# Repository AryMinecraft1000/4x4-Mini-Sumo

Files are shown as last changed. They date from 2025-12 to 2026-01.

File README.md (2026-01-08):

# 4x4-Mini-Sumo
A 4x4 mini sumo robot to fit in the 10x10cm, 500g class.
I chose this design philosophy as I've built 2 wheel drive international competition winning robots before and I wanted to challenge myself with the added complexity and space restrictions of a 4x4 robot. I also want to use this design to compete im my local international competition this spring.

I'd like to note that this is **NOT a battlebot**, its a far **more complex** robot witch uses sensors and **advanced code** to execute its task (Unlike battlebots which are just rc cars with weapons). It is part of one of the most competitive classes in international robotics where the top robots cost well over 1000$.





The Jsumo PCB has wiring intructions written on it.



# Bill of Materials: Mini Sumo Robot Project

| Part Name | Unit Price (USD) | Qty | Total Price (USD) | URL |
| :--- | :---: | :---: | :---: | :--- |
| **Jsumo XMotion** All In One Controller V3 | $44.95 | 1 | $44.95 | [Link](https://www.jsumo.com/xmotion-robot-controller) |
| **Jsumo Mini Katana Blade** (10cm) | $4.95 | 2 | $9.90 | [Link](https://www.jsumo.com/mini-katana-blade-for-mini-sumo-robot-10cm) |
| **Jsumo JS40F** Digital Distance Sensor | $12.50 | 4 | $50.00 | [Link](https://www.jsumo.com/js40f-digital-infrared-ir-distance-sensor-min-40-cm-range) |
| **Jsumo JS2622S** Steel-Silicone Wheel Pair | $14.50 | 2 | $29.00 | [Link](https://www.jsumo.com/js2622-steel-silicone-wheel-pair-26mm-diameter) |
| **Generic 050 Motor** | $5.00 | 4 | $20.00 | [Link](https://www.aliexpress.com/item/1005008126068612.html) |
| **QRE1113 IR Reflection Sensor** | *Region Dep.* | 2 | $0.00* | [Link](https://www.aliexpress.com/item/1005005682098178.html) |
| **LiPo Battery** (Locally Sourced) | $20.00 | 1 | $20.00 | - |
| **Total Project Items** | - | - | **$173.85** | - |

---

### 📦 Final Cost Breakdown

| Description | Amount (USD) |
| :--- | ---: |
| Imported Jsumo Subtotal | $133.85 |
| Jsumo Shipping | $46.95 |
| Import Tax (23% of $180.80) | $41.58 |
| AliExpress Parts & Shipping | $35.00 |
| Local Battery (Exempt) | $20.00 |
| **GRAND TOTAL** | **$277.38** |

> [!NOTE]
> *The 23% import tax is only applied to Jsumo items and their respective shipping. AliExpress and local items are added as flat costs.

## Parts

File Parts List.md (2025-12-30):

For this project you will need:
- All the parts in the BOM
- All the 3D printed parts in the CAD file in their specified quantities
- one 2mm diamater axel between 35-50mm in length **(50mm recomended)**
- at least 1 spring with a **maximum lenght** of 11mm
- wires, however more than enough should be included with the Jsumo sensors
- conectors for the battery, **JST prefered** (one set, male and female)
- 8x 19mm long M3 screws for the motor covers/mounts **(thread lenght)**
- 4x 9mm long M2 screws for mounting the front walls **(thread lenght)**
- 2x 12mm long M2 screws for the whing-blade mechanism **(thread lenght)**
- 2x 6mm long M2 screws for mounting the front cover **(thread lenght)**
- 2x 4mm long M2 screws for mounting side sensors **(full lenght)**
- 2x 5mm long M2 screws for mounting front sensors **(full lenght)**
- 4x M2 nuts

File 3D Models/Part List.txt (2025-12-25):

Blade Bracket -> 1
Front Plate -> 1
IR Sensor Holder 1 -> 2
IR Sensor Holder 2 -> 2
Front Wall L -> 1
Front Wall R -> 1
Motor Cover -> 4
Chassis -> 1

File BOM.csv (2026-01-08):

Item | Description | Quantity | Unit Price ($) | Total Price ($) | URL
Jsumo XMotion | All In One Controller V3 | 1 | 44.95 | 44.95 | https://www.jsumo.com/xmotion-robot-controller
Jsumo Katana Blade | 10cm Mini Sumo Blade | 2 | 4.95 | 9.90 | https://www.jsumo.com/mini-katana-blade-for-mini-sumo-robot-10cm
Jsumo JS40F | Digital Distance Sensor | 4 | 12.50 | 50.00 | https://www.jsumo.com/js40f-digital-infrared-ir-distance-sensor-min-40-cm-range
Jsumo JS2622S | Steel-Silicone Wheel Pair | 2 | 14.50 | 29.00 | https://www.jsumo.com/js2622-steel-silicone-wheel-pair-26mm-diameter
050 Motor | Generic DC Motor | 4 | 5.00 | 20.00 | https://www.aliexpress.com/item/1005008126068612.html
QRE1113 IR Sensor | Infrared Reflection Sensor | 2 | Depending on Region | 0.00 | https://www.aliexpress.com/item/1005005682098178.html
AliExpress Shipping | Shipping for Motors/Sensors | 1 | 15.00 | 15.00
Jsumo Shipping | International Shipping Fee | 1 | 46.95 | 46.95
Import Tax | 23% Import Duty (Jsumo Only) | 1 | 41.58 | 41.58
LiPo Battery | Locally Sourced Battery | 1 | 20.00 | 20.00
FINAL TOTAL |  |  | 277.38

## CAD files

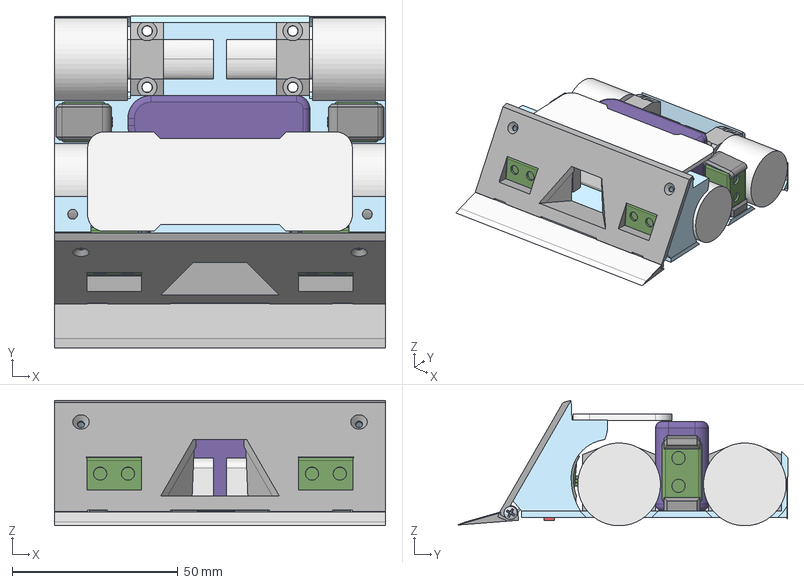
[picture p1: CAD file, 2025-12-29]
3D Models/4x4 Mini Sumo.step
100.0 x 100.2 x 37.9 mm
RR Motor
Part 1-Mirrored
RF Motor
Blade x 2
Chasis Base
XmotionV3
LR Motor
370mah 3s LiPo
IR Sensor Holder x 2
JS40F Digital Distance Sensor x 4
Line Sensor x 2
LF Motor
IR Sensor Holder 2 x 2
PH Pan head screw M2x0.40 x 16 x 2
Hex nut grade A & B M2x0.4 x 2
Blade Bracket Ver 2
torsion spring
Plow Shaft
Front Plate

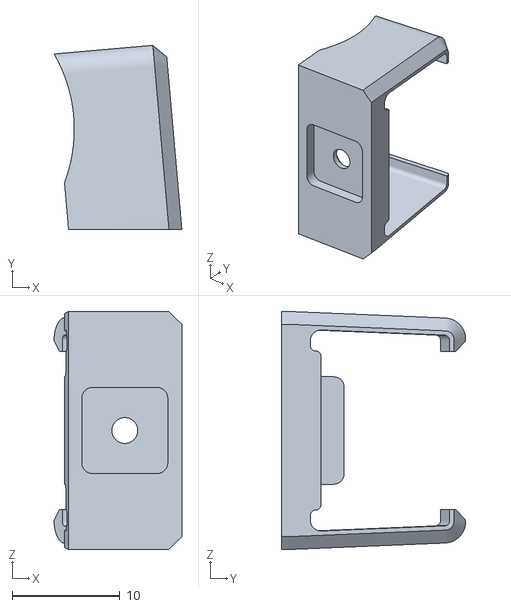
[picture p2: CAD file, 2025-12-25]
3D Models/IR Sensor Holder 2.stl
11.9 x 17.1 x 22.1

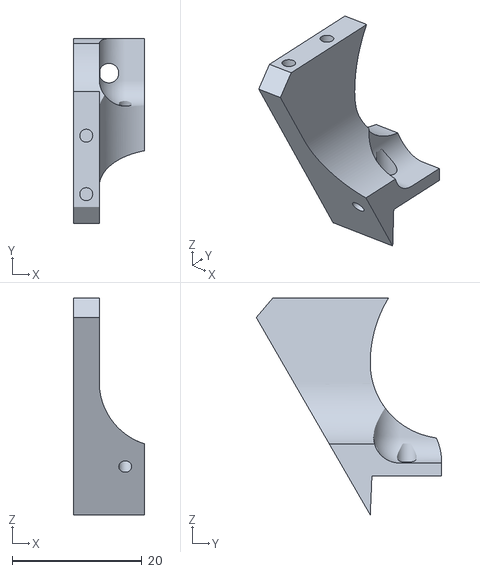
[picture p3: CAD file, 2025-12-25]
3D Models/Front Wall L.stl
11.0 x 28.6 x 33.4

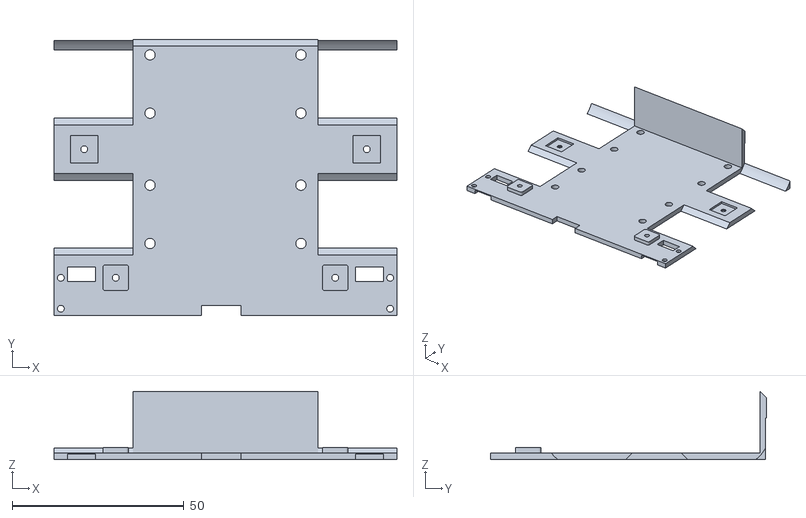
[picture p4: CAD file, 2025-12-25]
3D Models/Chassis.stl
100.0 x 80.5 x 19.9

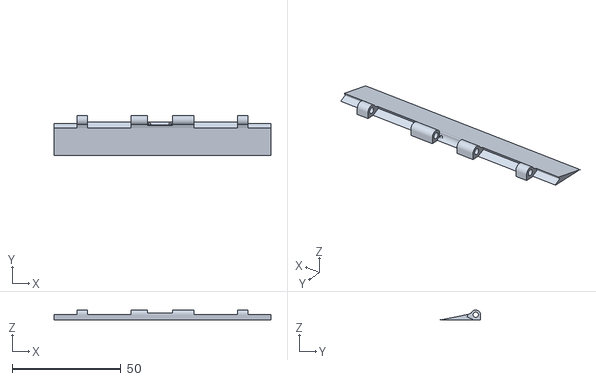
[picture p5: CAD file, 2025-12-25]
3D Models/Blade Bracket.stl
100.0 x 18.4 x 4.60

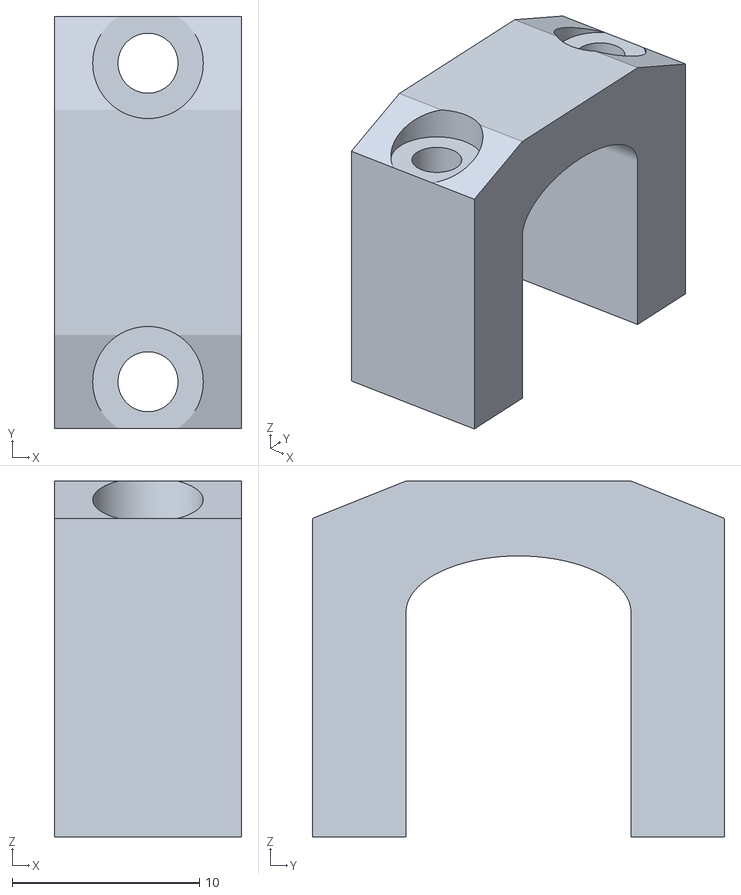
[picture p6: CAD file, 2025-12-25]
3D Models/Motor cover.stl
10.0 x 22.0 x 19.0

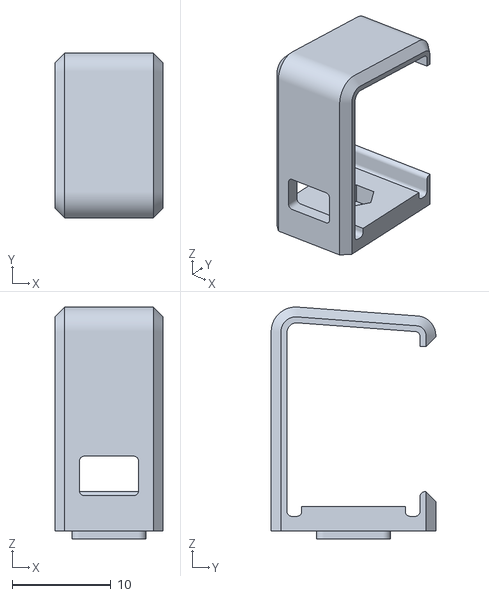
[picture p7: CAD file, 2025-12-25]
3D Models/IR Sensor Holder 1.stl
11.0 x 16.7 x 23.5

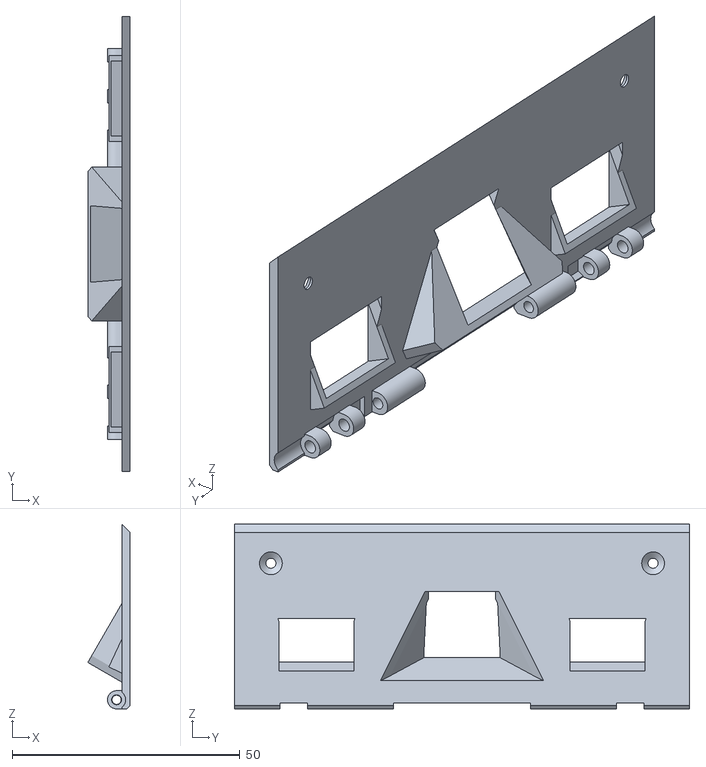
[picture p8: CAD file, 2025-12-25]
3D Models/Front Plate.stl
9.33 x 100.0 x 40.6

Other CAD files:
3D Models/Front Wall R.stl

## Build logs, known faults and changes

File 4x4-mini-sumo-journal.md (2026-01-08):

# Total Time Spent: 76 Hours
<!--
  This journal is auto generated by Hack Club Blueprint.
-->

## 12/15/2025 - Made chassis base, front walls and plate, blade mechanism  

_Time spent: 5.0h_  

3D designed the chassis, motor positions, front plate and spring based blade mechanism. This took some time to design the plow mechanism and the mounting solutions as the **size restrictions** a quite a pain.
	I used **Onshape** to model all the parts so far. I've had a bit of trouble fitting everything, however I got it to work in the end.



## 12/16/2025 - Research and Mounting solutions  

_Time spent: 6.0h_  

- Developed mounting solutions for the motors. I chose the 050 motor standard as it delivers good **speed** and **power** for its size. 
- **Researched** distance/opponent sensor options and developed mounting solutions for the current choice: The Jsumo JS40F Digital Distance Sensor. While not the best option, this distance sensor offers good price to performance and allows room for future improvements with better sensors and/or upgraded general elements.
- Cut out space for 2 line sensors witch will detect when the robot is about to leave the ring.



## 12/17/2025 - Modifications/improvements  

_Time spent: 5.5h_  

- Added front and rear blades to prevent pushing and achieve better contact with the ring. The design required some **major changes** to fit the 2 blades as the 100x100mm size limitation requires tight tolerances to maximize space.
- improved wheel protection
- revised spring loaded blade mechanism. 
- adjusted sensor positions to allow for a bigger battery, for now I have chosen a 3 cell LiPo as 12V will suffice for now. A 4 cell battery is an option for future versions.

The current robot only includes 2 front sensors allowing for another 2 diagonal, cross eyed sensors (If i can get them to fit)





Next I need to see which parts I have/can salvage and what I need to order to test the main hinged blade assembly as it is one of the most important parts for this robot to work

## 12/18/2025 12 AM - Improved general aspects and added a PCB solutions  

_Time spent: 5.0h_  



- Added possible battery position witch might get altered to fit sensors (ex: gyroscope, motor temperature sensor etc.)
- Improved front protection by extending the front walls to cover the wheels better. This proved to be a **huge pain** as the screw holes moved when any changes were made due to Onshapes handling of sketches.
- added possible PCB mounting position for the **XmotionV3** All In One Controller or the **RedNova V2** Robot Controller Board
I chose these PCBs as they include everything needed (microcontroller, motor drivers, sensor pinouts etc.). However, the RedNova V2 allows for higher voltages and amperages. As such it might be better for this use case.

XmotionV3:


RedNova V2:


## 12/18/2025 11 PM - Parts list and more sensor options  

_Time spent: 5.0h_  

- after **thorough** research I made a **preliminary** parts list (it will get modified over the next couple days) witch I will add to the GitHub once its done. All same-color parts can be inter swapped **except** the the **Sensor S** (cross-eyed diagonal sensors of witch **at least 2 are needed** in the current design, witch again may be changed). The suppliers in this parts list were carefully chosen based on my personal experience working with (most of) them in the past and promising specifications of their components.



- Found some smaller sensors witch would fit better as cross-eyed, diagonal sensors (Sensor S)



## 12/22/2025 12 AM - Front plate modifications and Lidar resarch  

_Time spent: 4.0h_  

- Modified front plate to remove excess material, some might get added back for PCB protection.



- Found a very interesting lidar sensor witch would perfectly fit our use case, this lidar is also quite cheap and would add a **significant competitive advantage**. It would replace the 2 cross-eyed sensors witch are currently **out of stock**. Opting for angling the 2 current front sensors to achieve diagonal view. It also possesses an **impressive** specification sheet witch is only accessible on request and took some time to obtain.



## 12/22/2025 2 PM - Preparing for real-world tests  

_Time spent: 4.0h_  

- Modified general robot aspects for easier 3D printing and altered front plate to better fit sensors. This was a true challenge as the limited size available for the robot required precise adjustments as to keep protection of the sensors.
- Prepared the 3D printer (general maintenance, filament drying, etc.)
- Imported the 3D models into the slicer.



- Gathered dummy mechanical parts for fitting tests (screws, dead motors, axels, dead blades, springs, etc.)



## 12/22/2025 6 PM - Printed prototype and fitted test parts  

_Time spent: 4.0h_  

- Printed and post processed test parts

WhatsApp Image 2025-12-22 at 18.14.07
WhatsApp Image 2025-12-22 at 18.14.07 (1)

- Assembled chassis and fitted motors, line sensor and battery (**only for test fitting**, as they have the **wrong performance specs**). I have also found out that I made a small error when making the motor holders and left about 1mm of extra space which I will fix in the next version.

WhatsApp Image 2025-12-22 at 18.14.07 (5)

- Tested swinging blade mechanism and test fitted the springs. The springs will need adjustments in the future for a better fit, however, they proved that this design is feasible and has **high potential**.

WhatsApp Image 2025-12-22 at 18.34.02 (1)WhatsApp Image 2025-12-22 at 18.34.02

 I encountered some issues while post processing witch slightly damaged one of the sensor holders, however it hasn't caused any issues in the test fit.
 For now I don't have the right M2 length screws and I had to use what I had on hand. It won't cause any issues for now as this is only a test to ensure we have enough space for all the components.  

## 12/23/2025 - Blade mechanism hardware and design alterations  

_Time spent: 3.5h_  

- Modified the blade mechanism to fit 2 springs instead of 1.
- Bent and modified the springs to fit in the plow mechanism. Who knew bending spring steel in such a way as to keep a desired shape wouldn't be that easy? After an annoying amount of abuse towards my fingers I managed to get **both springs** in the desired shape.
- Modified some of the mounting holes to allow press-fitting of the axel on which the springs sit on.


## 12/25/2025 - Code and GitHub  

_Time spent: 10.0h_  

 For code we will use our own custom code witch we have developed over the **past year**. However due to the **high competitive nature** of the **mini sumo competitions** we cannot share it publicly. **We will** release a simpler code in the GitHub based on the XmotionV3 library. This code will allow strategies and precise control of the robot at a professional level as it is quite similar to our old second-place winning code at international competitions.
 I have also made the GitHub with some of the the 3D models, preliminary code and BOM.



## 12/27/2025 6 PM - Line Sensors  

_Time spent: 4.0h_  

 To avoid leaving the fighting ring accidentally I have added the 2 line sensors in the design. These will allow for **multiple scenarios** (both sensors see the line, only one etc.).
 I have soldered and tested **multiple options** and settled on some cheap Chinese sensors I had lying around, these offer decent performance while being quite **inexpensive**. Its worth noting that many other teams use these sensors in their robots and their (quite expensive) robot kits and as such, these sensors have become a kind of standard.
 The soldering was a true pain as my soldering iron broke and I had to use a cheap chinese one that barely heats up.


## 12/27/2025 7 PM - Robot Materials  

_Time spent: 3.0h_  

 I have researched various materials for the robots chassis and other elements and I have reached the conclusion that all of the parts (apart from the chassis) should be 3D printed ASA/CF-Nylon. The chassis should be made out of a heavier material, to improve the center of gravity. The current **best option** is 3D printed **stainless steel** which JLC3DP has as an option for a quite affordable price (considering the fact that its 3D printed steel).



## 12/28/2025 12 AM - Time of flight sensors  

_Time spent: 4.0h_  

 I tested some small time of flight sensors to help fix the space issues however these proved to be too complex for our current design. They might be feasible in the future, I tried for **hours** to connect them. After talking to some of my friends witch go to my local university I found out that they require a special program and a multiplexer to work properly.
 If we could get these sensors to work in the future we would cut down **massively** on the space required.



## 12/28/2025 6 PM - PCB mounting solution  

_Time spent: 2.0h_  

 As **multiple** PCB options are available I wont make a fixed method to mount it. Instead I have developed a ingenious solution involving zip tying the PCB to the front walls, this will allow **many** different PCB solutions which will be held by the zip ties and the tension from the existing cables.



## 12/29/2025 2 PM - Added the 2 line sensors  

_Time spent: 1.0h_  

- Added the 2 line sensors to the 3D model. I have left quite a large margin of error so other versions of this sensor (different bakeout boards, etc.) fit. In the current design the sensor will be mounted with double sided tape as the sensor is quite light and using the screw holes already provided would be **overkill**.



## 12/29/2025 5 PM - GitHub finalization and Parts  

_Time spent: 3.0h_  

I have made the final changes to the GitHub as to abide by all the requirements. This took some time as I haven't really used GitHub and it proved to be quite annoying to learn. I have also added photos of the Jsumo Shopping cart in this journal.



I can't add photos of shopping carts for the battery (as it is locally sourced) and other small parts as they are scrapped from pens, random hinges, other old projects etc. However I included all of them in the BOM (I don't think i forgot anything)  

## 1/6/2026 - Weight and esthetic design  

_Time spent: 2.0h_  

- Calculated approximate final weight of the robot witch ends up weighing about 300 grams with a plastic 3D printed chassis and 400 grams with a stainless steel chassis.
- Added materials and color to all the parts to simulate the final look of the robot



## 1/7/2026 2 PM - Researched cheaper motors as replacements and IMPORTANT note  

_Time spent: 2.0h_  

- researched cheaper motors as per reviewer instructions. These will severally hinder performance



I'd like to note that this is **NOT a battlebot**, its a far **more complex** robot witch uses sensors and **advanced code** to execute its task (Unlike battlebots which are just rc cars with weapons). It is part of one of the most competitive classes in international robotics where the top robots cost well over 1000$. Also designing my own PCB is quite a bad idea as the Jsumo one has **over 8 years** of research and development behind it, however I can try and make one although I suspect the price wont be much more advantageous considering the technical challenges. 
**Catastrophic failure** of the PCB is not out of the question as I have no experience in PCB design and starting with such high voltages and amperages doesn't sound like a good idea.

## 1/7/2026 11 PM - GitHub Prices and items  

_Time spent: 1.0h_  

I added the cheaper (and much worse preforming) motors to all of the GitHub parts lists. These motors are substantially worse than the older options however I was instructed to reduce the overall price by the reviewer. I'd like to note to anyone interested in building my design that there are far better motors available with impressive torque figures for their RPM. And that the chinese motors will deliver worse performance.



## 1/8/2026 - GitHub changes and PCB research  

_Time spent: 2.0h_  

- Added shipping fees for the AliExpress items to the GitHub, the prices will vary by region.
- Researched some of the components and due to their high safety standards and due to the fact that we wont be buying the components in bulk the components for the custom PCB will be **more expensive** than buying a premade one.



(these are just some of the electronics needed)

- Using cheaper parts will turn the PCB into a **fire hazard**. Even if using premade parts is discouraged making my own without the **years** of research and development is **dangerous** and a **waste of money**.
- To further reduce costs I also abandoned the idea of a metal 3D printed chassis (Which would greatly help the center of gravity and resorted to a standard FDM printed chassis)  

I can't add photos of shopping carts for the battery (as it is locally sourced) and other small parts as they are scrapped from pens, random hinges, other old projects etc. However I included all of them in the BOM (I don't think i forgot anything)

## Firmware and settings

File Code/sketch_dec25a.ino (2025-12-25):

#include <Arduino.h>
#include <xmotionV3.h> 

int RightSensor = A3;
int FrontRightSensor = A5;
int FrontLeftSensor = A4;
int LeftSensor = A1;


int LeftLine = 1; 
int RightLine = 0;
int Start = A0;   

int motionDelay = 10;

int Led1 = 8;

int Dip1 = 5;
int Dip2 = 6;
int Dip3 = 7;


int Strategy = 0;

int LastValue = 0;

void setup() {
  xmotion.StopMotors(100); 
  xmotion.ToggleLeds(100);  
  pinMode(Led1, OUTPUT);
  pinMode(RightSensor, INPUT);
  pinMode(FrontRightSensor, INPUT);
  pinMode(FrontLeftSensor, INPUT);
  pinMode(LeftSensor, INPUT);
  pinMode(Start, INPUT);
  Serial.begin(9600);
}


void loop() {

  xmotion.StopMotors(1);
  

  while (digitalRead(Start) == 0) { 

    if (digitalRead(LeftSensor) == 1 || digitalRead(FrontLeftSensor) == 1 || 
        digitalRead(FrontRightSensor) == 1 || digitalRead(RightSensor) == 1) {
      digitalWrite(Led1, HIGH);
    } else {
      digitalWrite(Led1, LOW);
    }
    xmotion.UserLed2(100);
  }
  
 
  xmotion.CounterLeds(1000, 0);
  

  while (digitalRead(Start) == 1) { 
  
    if (digitalRead(LeftLine) == 0 && digitalRead(RightLine) == 1) {
    
      xmotion.Backward(50, 200);  
      xmotion.Right0(25, 400);     
    } 
    else if (digitalRead(LeftLine) == 1 && digitalRead(RightLine) == 0) {
     
      xmotion.Backward(50, 200);   
      xmotion.Left0(50, 400);     
    } 
    else if (digitalRead(LeftLine) == 0 && digitalRead(RightLine) == 0) {

      xmotion.Backward(50, 400);   
      xmotion.Right0(50, 400);     
    }
    
    
    else if (digitalRead(FrontLeftSensor) == 1 && digitalRead(FrontRightSensor) == 1) {
      xmotion.Forward(100, motionDelay); 
      LastValue = 0;
    }
    else if (digitalRead(FrontLeftSensor) == 1) {
      if(digitalRead(Dip1) == 1 && digitalRead(Dip2) == 0 && digitalRead(Dip3) == 0){
         xmotion.ArcTurn(50, 100, motionDelay);
         Strategy = 1;
      }
      else{
         xmotion.ArcTurn(10, 100, motionDelay);
         Strategy = 0;
      }
      LastValue = 3;
    }
    else if (digitalRead(FrontRightSensor) == 1) {
      if(digitalRead(Dip1) == 1 && digitalRead(Dip2) == 0 && digitalRead(Dip3) == 0){
         xmotion.ArcTurn(100, 50, motionDelay); 
         Strategy = 1;
      }
      else{
         xmotion.ArcTurn(100, 10, motionDelay);
         Strategy = 0;
      }
      LastValue = 4;
    } 
    else if (digitalRead(RightSensor) == 1) {
      xmotion.Right0(100, motionDelay); 
      LastValue = 1;
    }
    else if (digitalRead(LeftSensor) == 1) {
   
      xmotion.Left0(100,  motionDelay); 
      LastValue = 2;
    }
 
    else if (LastValue == 0) {
      xmotion.Forward(70, motionDelay);
    } 
    else if (LastValue == 1) {
      xmotion.Right0(100, motionDelay);
    } 
    else if (LastValue == 2) {
      xmotion.Left0(100, motionDelay); 
    } 
    else if (LastValue == 3) {
      if(Strategy == 1){
        xmotion.ArcTurn(50, 100, motionDelay);
      }
      else{
        xmotion.ArcTurn(10, 100, motionDelay);
      }
      
    } 
    else if (LastValue == 4) {
            if(Strategy == 1){
        xmotion.ArcTurn(100, 50, motionDelay);
      }
      else{
        xmotion.ArcTurn(100, 10, motionDelay);
      }
    }
    

  }
  
  xmotion.StopMotors(100);
}

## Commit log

2025-12-24 Update README with project details and cost breakdown
    Added design philosophy, images, and bill of materials for the mini sumo robot project.
2025-12-25 Add BOM for Mini Sumo Robot Project
    Added a Bill of Materials for the Mini Sumo Robot Project, including part names, prices, quantities, and a final cost breakdown.
    [BOM.csv]
2025-12-25 Revise financial summary and tax notes
    Updated financial summary section for clarity and formatting.
    [BOM.csv]
2025-12-25 Convert BOM to CSV format and clean up content
    Updated BOM.csv to a CSV format and removed markdown syntax.
    [BOM.csv]
2025-12-29 Update BOM.csv with detailed itemized list
    [BOM.csv]
2025-12-29 Add URLs to BOM.csv items
    [BOM.csv]
2025-12-29 Update BOM.csv to remove tax column and add total
    Removed 'Running Total ($ with Tax)' column and added 'FINAL TOTAL' row.
    [BOM.csv]
2025-12-29 Fix FINAL TOTAL line in BOM.csv
    [BOM.csv]
2025-12-29 Update quantities and totals in BOM.csv
    [BOM.csv]
2025-12-29 Revise Bill of Materials and cost breakdown
    Updated the Bill of Materials with URLs and revised costs.
2025-12-29 Update README with IR Line Sensor details
    Added IR Line Sensor to the components list and updated notes regarding its pricing.
2025-12-29 Rename IR Line Sensor to QRE1113 IR Reflection Sensor
    Updated the sensor name from 'IR Line Sensor' to 'QRE1113 IR Reflection Sensor' and adjusted the note regarding pricing.
2025-12-29 Add QRE1113 IR Sensor to BOM and update total
    [BOM.csv]
2026-01-06 Update note on QRE1113 sensor pricing
    Clarified note about QRE1113 sensor pricing consistency.
2026-01-07 Update README to clarify robot's purpose and complexity
    Clarified the purpose and complexity of the robot, emphasizing it is not a battlebot but a sophisticated robot using sensors and advanced code.
2026-01-07 Update project costs and add Generic 050 Motor
2026-01-07 Update BOM.csv with new items and revised totals
    [BOM.csv]
2026-01-08 Update shipping fees and final total in BOM.csv
    [BOM.csv]
